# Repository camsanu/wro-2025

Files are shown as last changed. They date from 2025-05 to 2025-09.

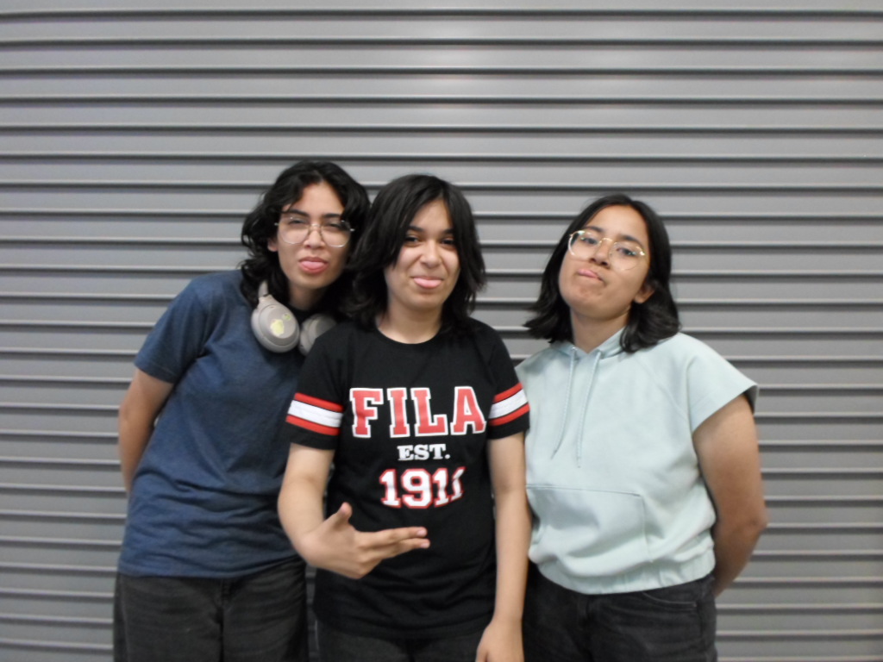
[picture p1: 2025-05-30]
t-photos/FUN.JPG

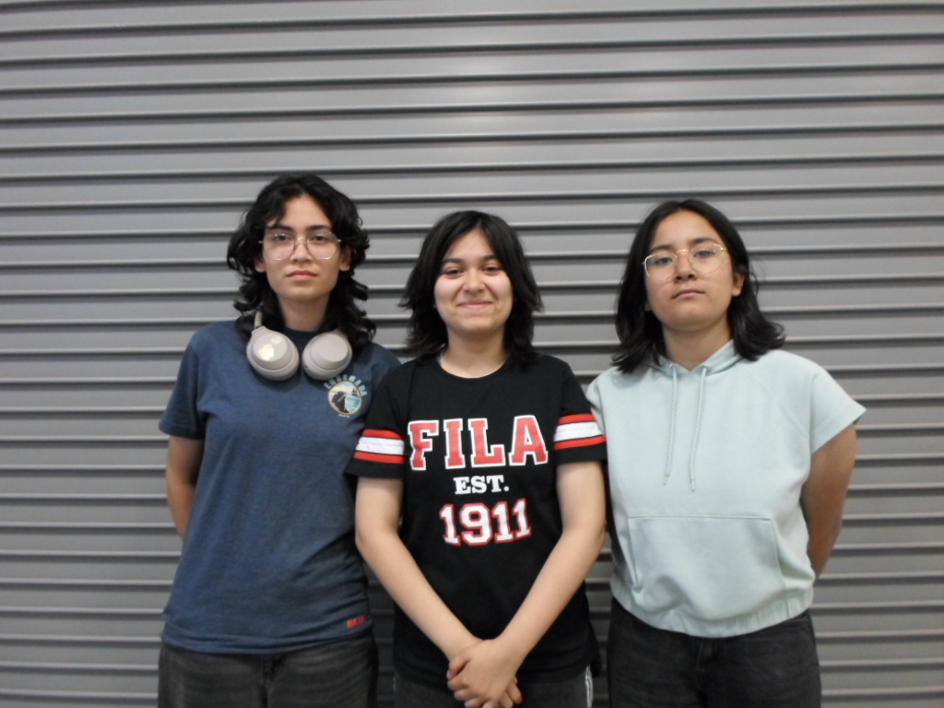
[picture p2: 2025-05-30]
t-photos/SRS.JPG

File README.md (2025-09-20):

Engineering materials
====

This repository contains all engineering materials for team Wired Wizards, from CETYS Universidad campus Mexicali as part of Sentinel Fox Engineering, competing on the WRO Future Engineers 2025 season, soon to go to the 2025 Mexican National.

## Team Members
* Yumian Del Mar Rodríguez Téllez
* Ahn Montserrat Salgado González
* Constanza Sandoval Ureña
* `Coach` Leonardo Daniel Médina Madrazo

## Content

* `models:` files used by 3D printers to produce the vehicle's chassis.   
* `schemes:` PDF schematic diagram illustrating the vehicle's circuitry.  
* `src:` code of control software for all components programmed to participate.  
* `t-photos:` 2 photos of the team (an official one and a funny photo).  
* `v-photos:` 6 photos of the vehicle (from every side, top and bottom).  
* `video:` video.md file with the link to a n second long driving demonstration.

# Solution

## Mechanism
For our prototype's motor, we used a DC motor gear system, where the motor is connected to a differential wrist mechanism that drives the back wheels and provides consistent, even movement. The front wheels do not receive any direct power from the motor, instead both the front wheels are hooked to the servo by a simple mechanism that we designed and 3d printed, with this we can proportionally steer the vehicle by turning both wheels at the same direction, at the same time.

## Electronic components
_For a more detailed explanation on the vehicle's circuitry, see [/schemes/README.md](./schemes/README.md)._
| Component  | Quantity |
| --- | --- |
| Arduino Uno  | 1  |
| Raspberry Pi 3  | 1  |
| Raspberry Pi Camera Module 2  | 1  |
| L298N Motor Driver | 1  |
| Hobby Gearmotor  | 1  |
| HC-SR04 Ultrasonic Sensor  | 3  |
| SG90 Micro Servo  | 1  |

The circuit is centered around our controller, the Arduino Uno, managing all components in the circuit to execute adequate responses. For navigation, we use three HC-SR04 Ultrasonic Sensors in order to use the measured distances as limits where the vehicle should react swiftly. Each sensor has its own echo and ground pin to avoid reliability issues, while sharing common power and trigger pins. Steering is managed by the SG90 Micro Servo, which provides precise 180-degree control, avoiding obstacles or staying in its route based on calculations from sensor data. To move the vehicle, an L298N motor driver hooked to a separate 9V battery powers and regulates the speed of the Hobby Gearmotor.

In order to identify the color of the obstacles and the parking, a Raspberry Pi 3 with a Raspberry Pi Camera Module detects objects through image processing. Applying color masks allows the Pi to see the object as a simple block and know its color, which it then communicates to the Arduino via USB serial communication. The Arduino then integrates the sensor and camera data to make quick decisions, such as amount of time it should steer or on what direction, allowing for precise maneuvering of the vehicle during rounds.

## Code
_For a more detailed explanation on the processes and logic behind the vehicle's source code, see [/src/README.md](./src/README.md)._

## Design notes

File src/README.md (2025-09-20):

Control software
===

This directory contains all code used for the controllers in the vehicle. Additionally, the `tests` folder contains simple, 
component-specific code to debug logic in the source code and verify the proper functioning of all components involved 
individually. Code is to be downloaded into the controllers by USB connection, for both the Arduino Uno and the Raspberry Pi.

# `src.ino`
Code uploaded to the Arduino Uno to control all sensors, motors and overall movement of the vehicle.
## Round Start and Parking
## Obstacle Identification
## Auto-Alignment
The vehicle is programmed to automatically go towards the middle lane of the track, independently of its starting position or orientation, as we see below: 

```c++
    // line 327
    fwd();
    saveDistances();
    printDistances();

    if(lDistance == rDistance){ // stay on the track's center lane by default
      myservo.write(sCenter);
    }
```

Naturally, the vehicle will start drifting from its straight line due to deformities on the track, wheels drifting, mistimed corner stops, etcetera, and if no corrections occur the vehicle might end up hitting obstacles or walls due to being miscalibrated. Therefore, we applied PID control in order to keep our servo's angle shifting enough to compensate. See the following code, which will be explained step by step:

```c++
// line 27
float Gp = 0.6; // proportional gain
float Gd = 1; // derivative gain
float Gi = 0.02; // integral gain
static float prevError = 0;
static float integ = 0;

// line 335
if(lDistance != rDistance && fDistance>threshold && (!red && !green)){ // check if vehicle is drifting away from center
      float error = rDistance - lDistance; // get error margin
      float deriv = error - prevError; // get change in error
      float servoAngle = sCenter + (Gp * error) + (Gd * deriv) + (Gi * integ); // pid control
      prevError = error;
      integ += error; // get cumulative error
      servoAngle = constrain(servoAngle, sMin, sMax); // limit angle to safe range
      integ = constrain(integ, -threshold, threshold); // limit integral windup
      if(lDistance > rDistance){ // print direction of overshoot for debugging
        Serial.println("Left Overshoot");
      }
      else if(rDistance > lDistance){
        Serial.println("Right Overshoot");
      }
      myservo.write(servoAngle);
    }
```
Starting off by variables, we have 5 variables that will determine how strongly each PID term affects the final angle:
```c++
// line 27
float Gp = 0.6; // proportional gain
float Gd = 1; // derivative gain
float Gi = 0.02; // integral gain
static float prevError = 0;
static float integ = 0;
```
The proportional gain reacts to how wide the current error is, that is, how offcenter the vehicle is at that moment; The derivative gain handles the change in error, supressing very sudden swings; The integral gain reacts to the sum of past errors, in order fix light offsets. These variables are necessary to make sure the correction isn't too relaxed offset builds up, nor too strict it slows down the vehicle by oscillating. The next two variables are static variables (that is, they keep their value through multiple loop iterations) that need to be updated to ensure the formula keeps working as intended.

## Steering

# `src.py`
Code uploaded to the Raspberry Pi to identify color obstacles and send this data to the Arduino Uno.

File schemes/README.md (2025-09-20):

# Schemes
On this directory you can find the schematic diagram for the vehicle's circuitry `scheme.pdf`, and an additional more visual 
one saved as `diagram.jpg`. We'll go into detail into the connections and functionality below.

## Arduino Uno
The main controller of the circuit. It receives the data from all other components on the circuit and determines what to do 
with it by following the corresponding programming (see [src/README.md](/src/README.md)). Its used pins are separated in two 
types, analog and digital, out of which we mainly use digital pins. The difference between them is digital pins allow for 
signals where a binary state is needed, meanwhile analog ones allow for continuous voltage output using PWM (Pulse Width 
Modulation).

## HC-SR04 Ultrasonic Sensors
The main navigation tool of the circuit, collecting distances by measuring the time it takes an emitted sound wave to bounce 
back into the sensor. The three of them have their own echo pins and grounds on the Arduino board, and they all share a power 
and trigger pin. The lack of common grounds for the sensors came about as we found out making them share a ground pin would 
often make the sensors go unresponsive due to unforeseen wiring issues, leading us to leaving them independent of each other.

## SG90 Micro Servo
The motor in charge of steering the vehicle into the right positions. It allows for precise angle orientation in a 180 degree 
span, making it so we are able to use formulas involving the distances taken with our ultrasonic sensors to derive the needed
angle at any given moment, whether it is to ensure the vehicle goes in a straight line, or to avoid crashing into walls or 
obstacles. Connecting the ground pin and the power pin to 5V, besides a connection to a PWM-enabled digital pin (in our case 
number 6) is enough to establish a proper connection to the Arduino.

## L298N Motor Driver
The regulator responsible for supplying enough power to move the motors, as the power the controllers can provide is not 
enough to support the full weight of the vehicle. The motor driver allows us to not only supply this additional power without
feeding it back into the circuit and risk damaging components running at lower voltages, but also to command the motor and
regulate its speed using the INPUT and ENABLE pins, which are connected to the Arduino.

## Raspberry Pi 3	
The computer vision of the circuit. The Pi Camera Module is plugged into the Raspberry Pi directly through its camera port, 
allowing for no-fuzz connection to the Pi. In the Pi (see [src/README.md](/src/README.md)) we execute code to apply masks over 
the captured image in order to derive the existence of specifically colored objects, those being the obstacles. The Pi then 
sends this data through serial communication by USB with the Arduino, who will then process it and react accordingly.

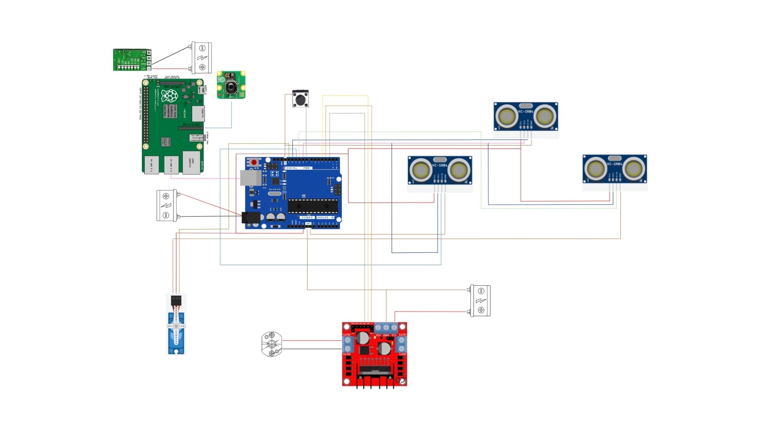
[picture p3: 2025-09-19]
schemes/diagram.jpg

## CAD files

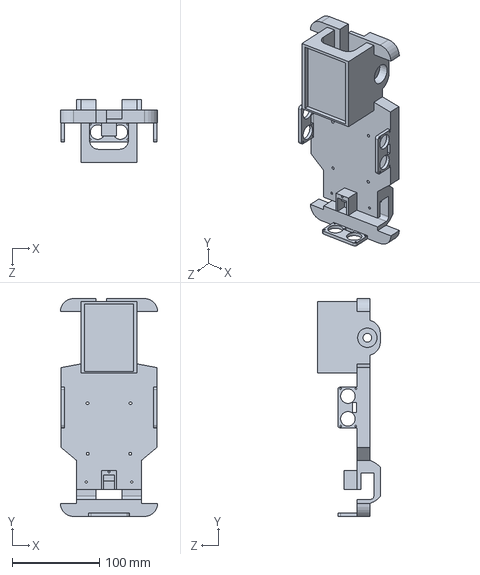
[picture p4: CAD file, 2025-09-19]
models/chassis/chassis.SLDPRT
111.5 x 249.9 x 72.0 mm

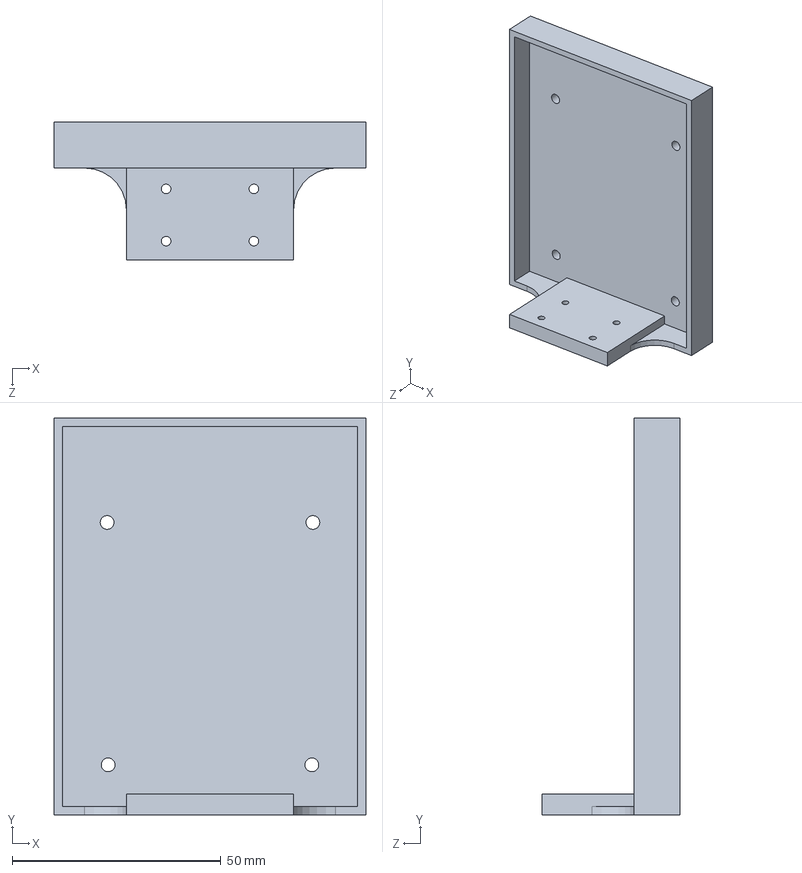
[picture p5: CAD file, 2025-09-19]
models/chassis/secondFloor.SLDPRT
74.5 x 95.0 x 33.0 mm

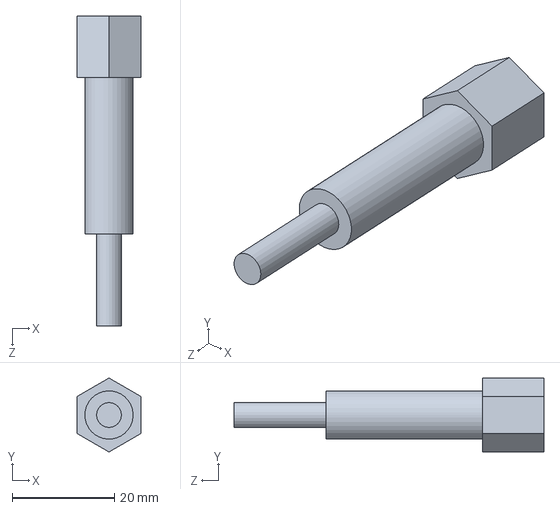
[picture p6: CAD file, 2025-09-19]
models/chassis/wheelAdaptorR.SLDPRT
12.5 x 14.4 x 60.5 mm

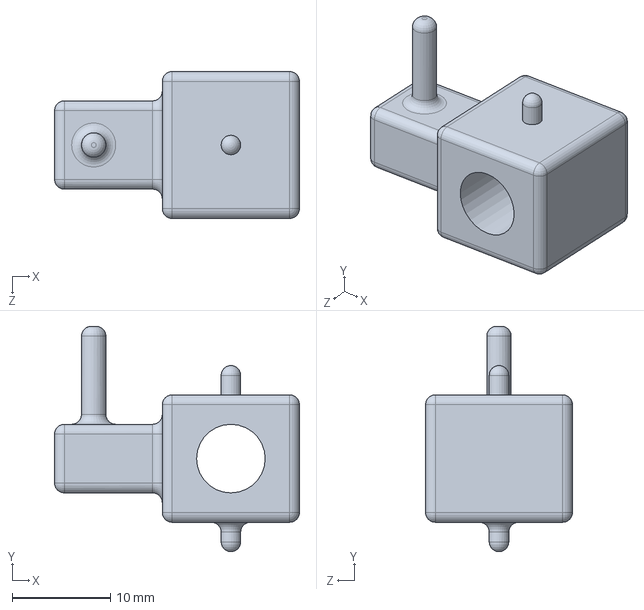
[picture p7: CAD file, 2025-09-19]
models/steering/mConnector.SLDPRT
25.0 x 23.0 x 15.0 mm

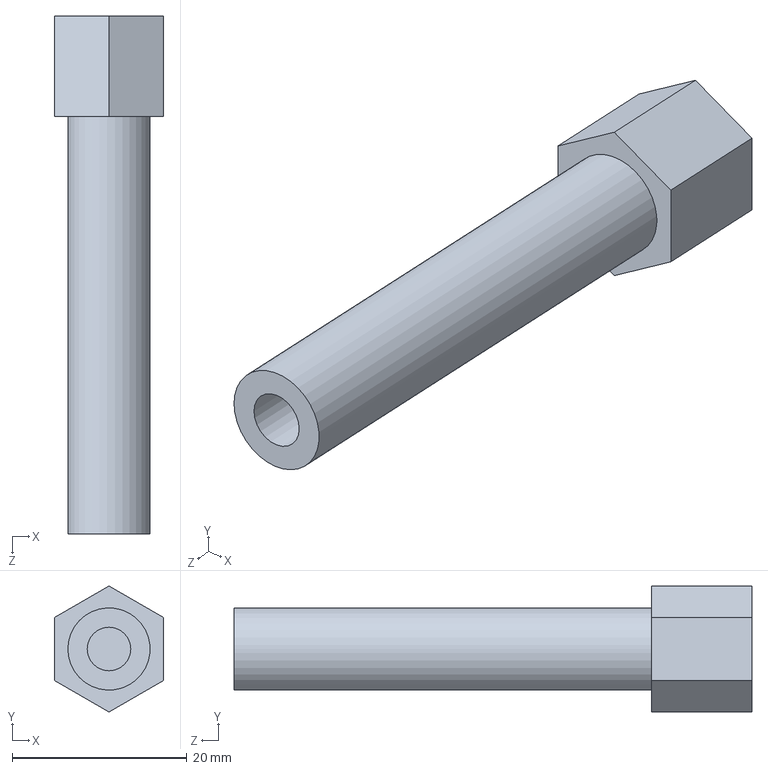
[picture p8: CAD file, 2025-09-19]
models/chassis/wheelAdaptorL.SLDPRT
12.5 x 14.4 x 59.3 mm

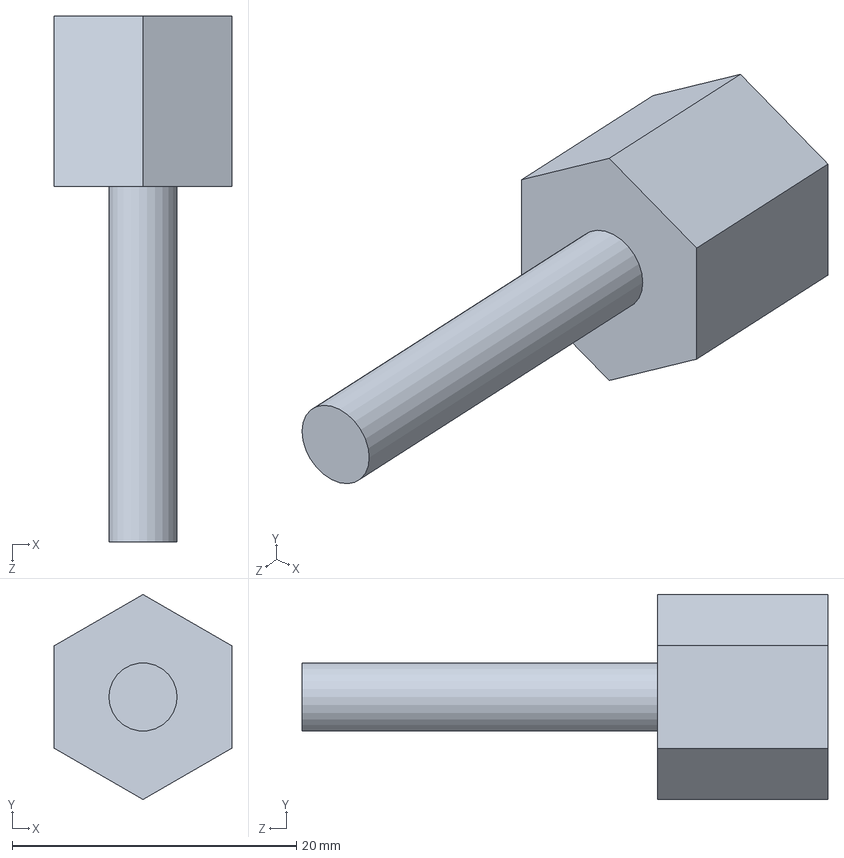
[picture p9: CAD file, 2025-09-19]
models/chassis/WFrontAdaptor.SLDPRT
12.5 x 14.4 x 37.0 mm

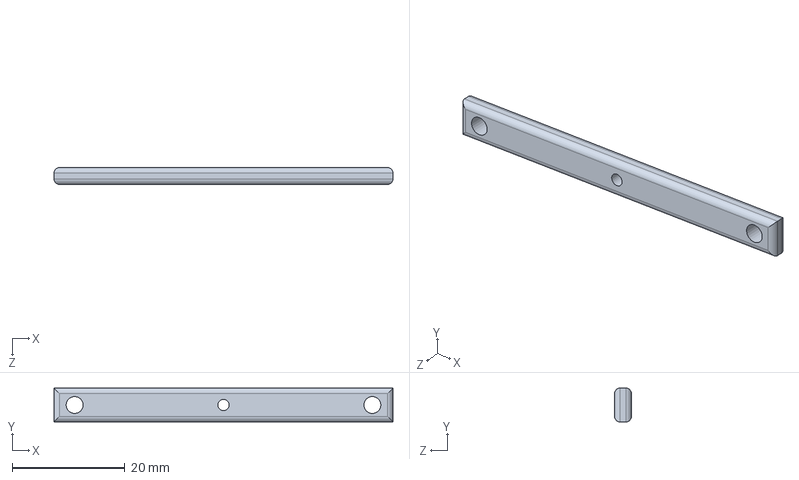
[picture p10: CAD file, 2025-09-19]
models/chassis/steerBar.SLDPRT
60.0 x 6.00 x 3.00 mm

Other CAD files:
models/steering/motorGear.SLDASM
models/steering/wheelsGear.SLDASM

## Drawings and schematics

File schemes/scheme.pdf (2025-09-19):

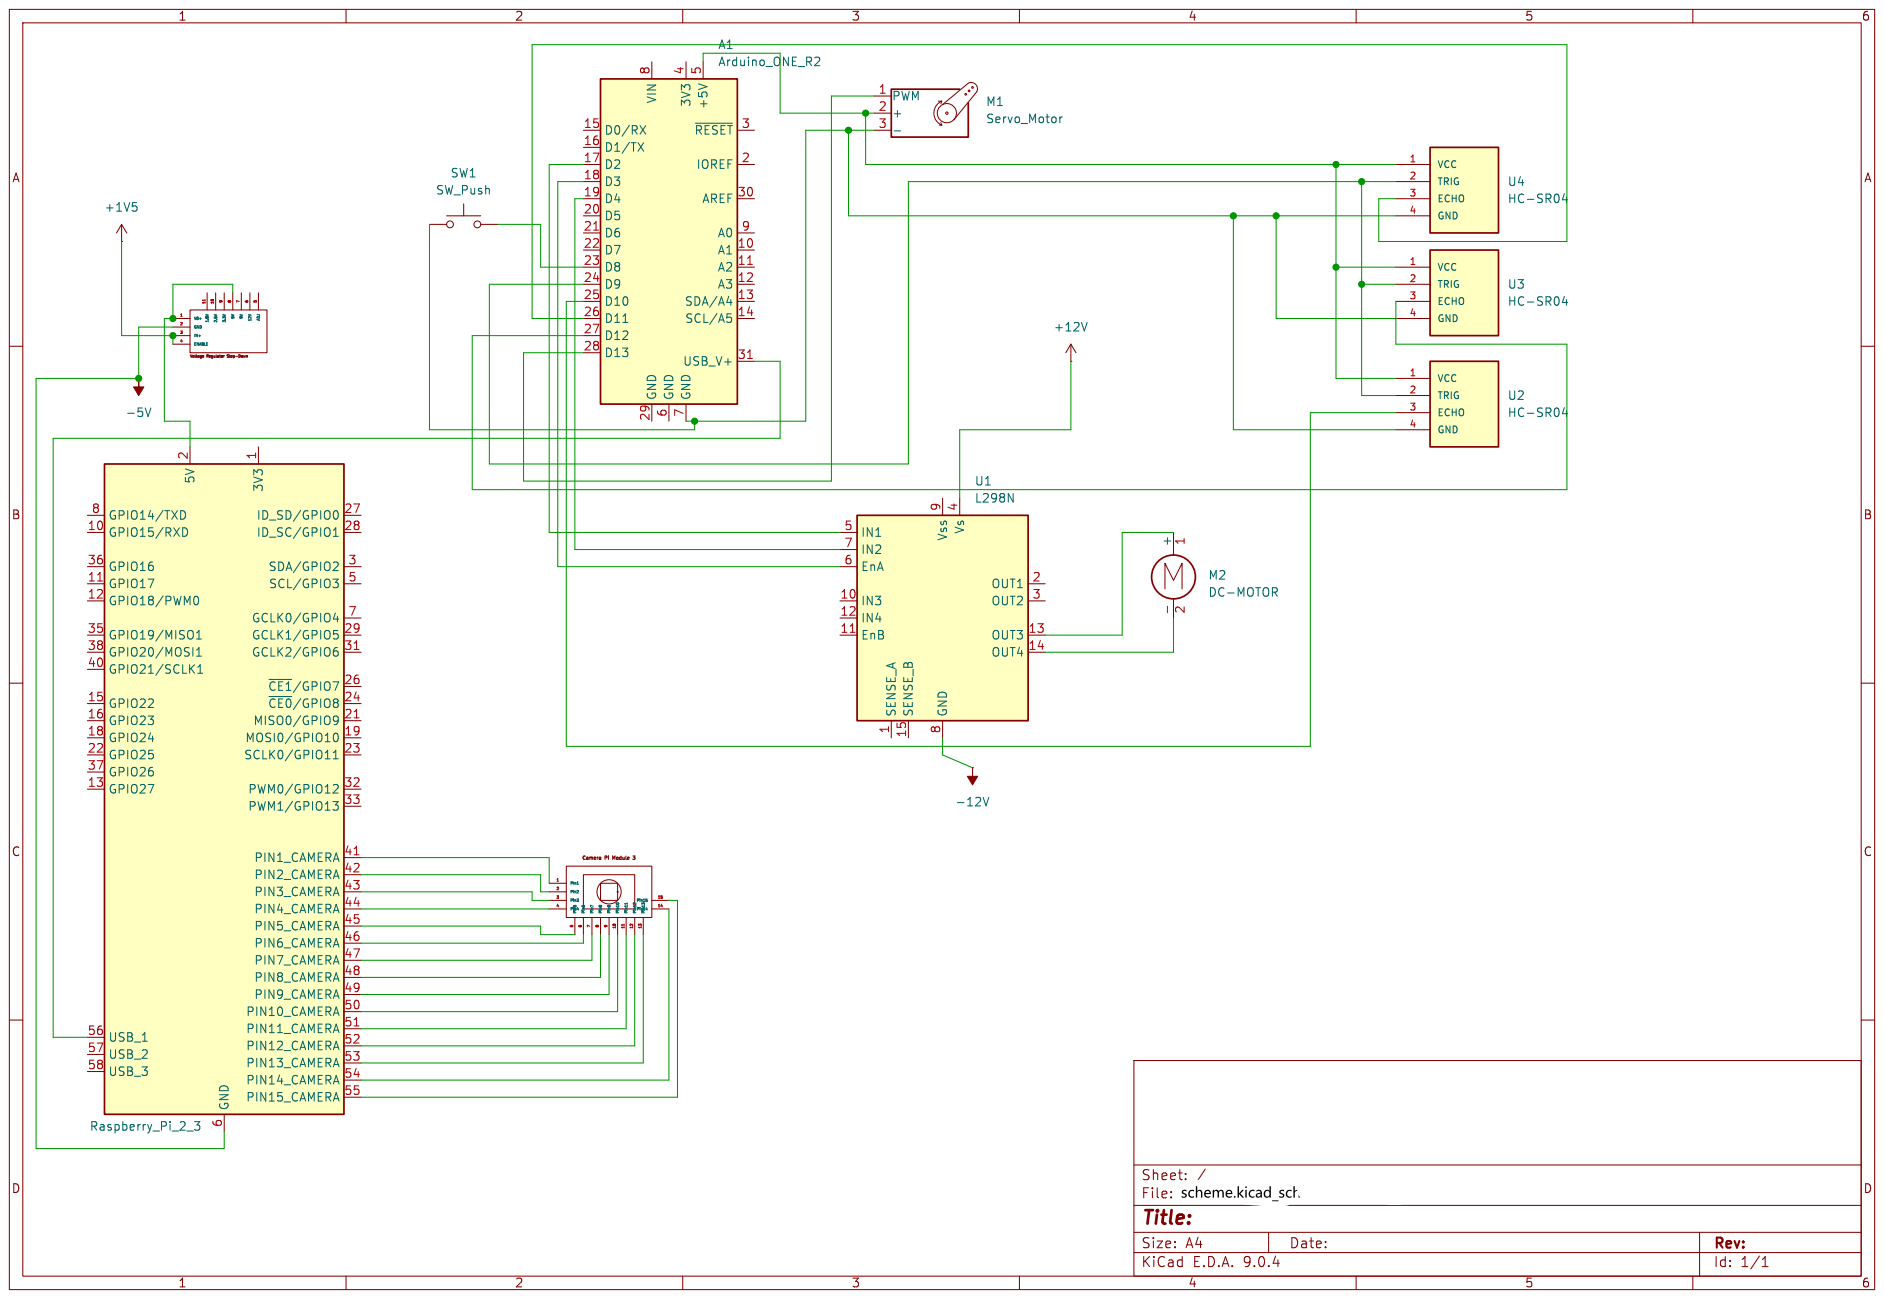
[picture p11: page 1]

IOREF 2 AREF 30 A0 9 A1 10 A2 11 A3 12 SDA/A4 13 SCL/A5 14 USB_V+ 31 A1Arduino_ONE_R2

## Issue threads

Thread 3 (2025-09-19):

Update schemes

camsanu, 2025-09-19:
1. Remove second gearmotor
2. Match pins to current vehicle
3. Remove second file (no longer necessary)

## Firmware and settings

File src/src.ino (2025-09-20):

#include <Servo.h>

Servo myservo;
const int sMin = 50, sMax = 130, sCenter = 90; // servo limits; left, right, center respectively

// motor pins
#define IN1  4
#define IN2  2 
#define ENA 3

// ultrasonic pins and distance variables (all distances are in cm)
const int trigPin = 12, echoPin_f = 11, echoPin_r = 10, echoPin_l = 9;
int lDistance, rDistance, fDistance;
float startL, startR, startF;
int numReadings = 3; // samples for reading averaging
const int threshold = 100; // threshold for turning
const float tolerance = 5.0; // tolerance for returning to initial position

// button variables
const int buttonPin = 8;
bool pushEd = false;
int pushEs = 0;
bool lastState = HIGH;

// pid control
int corners = 0, laps = 0;
float Gp = 0.6; // proportional gain
float Gd = 1; // derivative gain
float Gi = 0.02; // integral gain
static float prevError = 0;
static float integ = 0;

// object detection
bool red = false;
bool green = false;
bool parking = false;
int parks = 0; // initial or final parking

// distance and control functions
long getDistance(int echoPin){ // ultrasonic distance capture
    long duration;
    long sum = 0;

    for(int i = 0; i < numReadings; i++){
      digitalWrite(trigPin, LOW);
      delay(2);
      digitalWrite(trigPin, HIGH);
      delay(10);
      digitalWrite(trigPin, LOW);

      duration = pulseIn(echoPin, HIGH, 20000);
      sum += (duration * 0.034 / 2);
    }
  return sum / numReadings;
}

void saveDistances(){
  fDistance = getDistance(echoPin_f);
  lDistance = getDistance(echoPin_l); 
  rDistance = getDistance(echoPin_r);
}

void saveStart(){ // get initial position
  startF = getDistance(echoPin_f);
  startL = getDistance(echoPin_l); 
  startR = getDistance(echoPin_r);
}

void printDistances(){
  Serial.print("F ");
  Serial.print(fDistance);
  Serial.print("; L ");
  Serial.print(lDistance);
  Serial.print("; R ");
  Serial.println(rDistance);
}

// motor and movement control
void fwd(){
  digitalWrite(IN2, HIGH); 
  digitalWrite(IN1, LOW);
  analogWrite(ENA, 255);
}

void rev(){
  digitalWrite(IN2, LOW); 
  digitalWrite(IN1, HIGH);
  analogWrite(ENA, 255);
}

void dead(){
  digitalWrite(IN2, LOW); 
  digitalWrite(IN1, LOW);
}

void endP(){
  dead();
  myservo.write(sCenter);
  Serial.println("Over");
  for(;;);
}

void lTurn(){
  static unsigned long turnStart = 0;
  static bool turning = false;
  if(!turning){ 
    myservo.write(sMin); // turn left
    turnStart = millis(); // start timing turn
    turning = true;
    Serial.println("Turning Left");
  }

  if(millis() - turnStart >= 800){ // finish turn after set time
    if(lDistance < threshold){
      myservo.write(sCenter); // recenter
      corners++; // count corner as done
      Serial.println("Turned Left");
    }
    turning = false;
  }
}

void rTurn(){ // same as above
  static unsigned long turnStart = 0;
  static bool turning = false;
  if(!turning){
    myservo.write(sMax);
    turnStart = millis();
    turning = true;
    Serial.println("Turning Right");
  }

  if(millis() - turnStart >= 800){
    if(rDistance < threshold){
      myservo.write(sCenter);
      corners++;
      Serial.println("Turned Right");
    }
    turning = false;
  }
}

void redTurn(){ // red obstacle turn
  static unsigned long turnStart = 0;
  static bool turning = false;
  if(!turning){
    myservo.write(sMax); // turn right
    turnStart = millis(); // start timing turn
    turning = true;
    Serial.println("Avoiding Red");
  }

  if(millis() - turnStart >= 300){ // shorter set time than corner turns to make up for space
    if(rDistance < threshold){
      myservo.write(sCenter); // recenter
      Serial.println("Avoided Red");
      red = false; // reset red obstacle detection
    }
    turning = false;
  }
}

void greenTurn(){ // same as above
  static unsigned long turnStart = 0;
  static bool turning = false;
  if(!turning){
    myservo.write(sMin);
    turnStart = millis();
    turning = true;
    Serial.println("Avoiding Green");
  }

  if(millis() - turnStart >= 300){
    if(lDistance < threshold){
      myservo.write(sCenter);
      Serial.println("Avoided Green");
      green = false;
    }
    turning = false;
  }
}

void unparkLeft(){
  myservo.write(sMin);
  digitalWrite(IN2, HIGH); 
  digitalWrite(IN1, LOW);
  analogWrite(ENA, 200); // adjust speed for softer exit
  if(fDistance <= 10){ // avoid hitting wall
    dead();
  }
  Serial.println("Exiting Parking: Stage One");

  if(lDistance < rDistance){
    myservo.write(sMax); // turn right
    analogWrite(ENA, 255); // return to normal speed
    Serial.println("Exiting Parking: Stage Two");
  }
  if(lDistance == rDistance){
    myservo.write(sCenter); // recenter
  }
}

void unparkRight(){ // same as above
  myservo.write(sMax);
  digitalWrite(IN2, HIGH); 
  digitalWrite(IN1, LOW);
  analogWrite(ENA, 200);
  if(fDistance <= 10){
    dead();
  }
  Serial.println("Exiting Parking Stage One");
  
  if(lDistance > rDistance){
    myservo.write(sMin);
    fwd();
    Serial.println("Exiting Parking Stage Two");
  }
  if(lDistance == rDistance){
    myservo.write(sCenter);
  }
}

void parkLeft(){
    digitalWrite(IN2, HIGH); 
    digitalWrite(IN1, LOW);
    analogWrite(ENA, 200); // adjust speed for softer exit
    myservo.write(sMax); // turn right to enter
    if(fDistance <= 10){ // avoid hitting wall
      dead();
    }
    if(lDistance < rDistance){
      myservo.write(sMin); // adjust to get straight parking
      if(lDistance == rDistance){
        myservo.write(sCenter); // recenter
        dead(); // standby
      }
    }
}

void parkRight(){ // same as above
  digitalWrite(IN2, HIGH); 
  digitalWrite(IN1, LOW);
  analogWrite(ENA, 200);
  myservo.write(sMax);
  if(fDistance <= 10){
    dead();
  }
  if(lDistance < rDistance){
    myservo.write(sMin);
    if(lDistance == rDistance){
      myservo.write(sCenter);
      dead();
    }
  }
}


// setup function
void setup() {
  pinMode(IN2, OUTPUT);
  pinMode(IN1, OUTPUT);
  pinMode(ENA, OUTPUT);

  pinMode(trigPin, OUTPUT);
  pinMode(echoPin_f, INPUT);
  pinMode(echoPin_r, INPUT);  
  pinMode(echoPin_l, INPUT);
  pinMode(buttonPin, INPUT_PULLUP);

  myservo.attach(6);
  Serial.begin(9600);
  saveStart();
  dead();
}

// main loop
void loop() {
  bool buttonState = digitalRead(buttonPin);
  if(lastState == HIGH && buttonState == LOW){ 
    pushEs++;
    if(pushEs == 1){
      pushEd = true;
      Serial.println("Started");
    } else if(pushEs > 1){
      pushEd = false;
      Serial.println("Killed");
    }
    delay(50); // debounce
  }
  lastState = buttonState;

  if(pushEd){
    if(Serial.available() > 0){ // check for raspi color input
      char inChar = (char)Serial.read();
      if(inChar == 'R'){
        red = true;
        Serial.println("R"); // respond to raspi input for debugging
      }
      else if(inChar == 'G'){
        green = true;
        Serial.println("G");
      }
      else if(inChar == 'M'){
        parking = true;
        Serial.println("M");
      }
    }

    if(parking && parks == 0){ // checks if inside parking
      parks++; // initial parking done
      if(lDistance > rDistance){
        unparkLeft();
      } else if(rDistance > lDistance){
        unparkRight();
      }
    }

    if(parking && parks == 1){ // checks if outside parking
      if(lDistance > rDistance){
        parkLeft();
      } else if(rDistance > lDistance){
        parkRight();
      }
      endP();
    }

    fwd();
    saveDistances();
    printDistances();

    if(lDistance == rDistance){ // stay on the track's center lane by default
      myservo.write(sCenter);
    }
  
    if(lDistance != rDistance && fDistance>threshold && (!red && !green)){ // check if vehicle is drifting away from center
      float error = rDistance - lDistance; // get error margin
      float deriv = error - prevError; // get change in error
      float servoAngle = sCenter + (Gp * error) + (Gd * deriv) + (Gi * integ); // pid control
      prevError = error;
      integ += error; // get cumulative error
      servoAngle = constrain(servoAngle, sMin, sMax); // limit angle to safe range
      integ = constrain(integ, -threshold, threshold); // limit integral windup
      if(lDistance > rDistance){ // print direction of overshoot for debugging
        Serial.println("Left Overshoot");
      }
      else if(rDistance > lDistance){
        Serial.println("Right Overshoot");
      }
      myservo.write(servoAngle);
    }

    // obstacle detection
    if(red || green){ 
      if(red){
        redTurn();
      }
      else if(green){
        greenTurn();
      }
    }

    if(fDistance < threshold && (!red && !green)){ // check if at open corner
      if(lDistance > rDistance){
        lTurn();
        integ = 0; // reset to avoid integral windup
      }
      else if(rDistance > lDistance){
        rTurn();
        integ = 0;
      }
    }
    
    if(corners == 4){ // reset corners after finishing lap
      laps++;
      corners = 0;
    }
  
    if(laps==3 && (!red && !green)){ // natural end, finished laps and no objects
      bool closeF = abs(fDistance-startF) <= tolerance; // checks if initial and current position are within tolerance range
      bool closeL = abs(lDistance-startL) <= tolerance;
      bool closeR = abs(rDistance-startR) <= tolerance;
      if(closeF && closeL && closeR){ // begin shut down
        static unsigned long shutStart = 0; 
        static bool shutting = false;
        if(!shutting){
          shutStart = millis();
          shutting = true;
          Serial.println("Shutting down");
        }
        if(millis() - shutStart >= 800){ // wait before shutting down
          Serial.println("Shut down complete");
          shutting = false;
          endP(); // end program
        }
      }
    }
  } 
  if(pushEd == false && pushEs > 1){ // kill switch
    endP();
  }
}

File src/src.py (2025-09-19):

import cv2
import numpy as np
import serial
from picamera2 import Picamera2, Preview

ser = serial.Serial('/dev/ttyUSB0', 9600, timeout=1)
picam = Picamera2()
cam_config = picam.create_preview_configuration(main={"format": 'XRGB8888', 'size': (640, 480)})
picam.configure(cam_config)
picam.set_controls({"FrameDurationLimits": (33333, 33333)})
picam.start_preview(Preview.NULL)
picam.start()

lowerGreen = np.array([45, 150, 150])
upperGreen = np.array([70, 255, 255])

lowerRed1 = np.array([170, 150, 150])
upperRed1 = np.array([180, 255, 255])
lowerRed2 = np.array([0, 150, 150])
upperRed2 = np.array([10, 255, 255])

lowerMag = np.array([140, 150, 150])
upperMag = np.array([160, 255, 255])

kernel = np.ones((5, 5), np.uint8)
sent = False

while True:
	frame = picam.capture_array()
	hsv = cv2.cvtColor(frame, cv2.COLOR_BGR2HSV)
	
	maskGreen = cv2.inRange(hsv, lowerGreen, upperGreen)
	maskGreen = cv2.morphologyEx(maskGreen, cv2.MORPH_OPEN, kernel)

	maskRed1 = cv2.inRange(hsv, lowerRed1, upperRed1)
	maskRed2 = cv2.inRange(hsv, lowerRed2, upperRed2)
	maskRed = cv2.bitwise_or(maskRed1, maskRed2)
	maskRed   = cv2.morphologyEx(maskRed, cv2.MORPH_OPEN, kernel)

	maskMag = cv2.inRange(hsv, lowerMag, upperMag)
	maskMag   = cv2.morphologyEx(maskMag, cv2.MORPH_OPEN, kernel)

	if not sent:
		if cv2.countNonZero(maskGreen) > 200:
			ser.write(b"G\n")
			sent = True
		elif cv2.countNonZero(maskRed) > 200:
			ser.write(b"R\n")
			sent = True
		elif cv2.countNonZero(maskMag) > 200:
			ser.write(b"M\n")
			sent = True
	else:
		if (cv2.countNonZero(maskGreen) <= 200 and 
			cv2.countNonZero(maskRed) <= 200 and 
			cv2.countNonZero(maskMag) <= 200):
			sent = False

	key = cv2.waitKey(1)
	if key == 27:
		break

picam.close()
ser.close()
cv2.destroyAllWindows()

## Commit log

2025-08-14 Add files via upload
    simple hello world for the arduino to make sure there are no larger hardware issues at hand
2025-09-19 Updated name
    [WFrontAdaptor.SLDPRT, chassis.SLDPRT, secondFloor.SLDPRT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]
